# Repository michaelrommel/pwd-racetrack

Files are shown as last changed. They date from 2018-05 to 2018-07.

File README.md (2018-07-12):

# pwd-racetrack
A Pinewood Derby racetrack timer and start gate electronics circuits + firmware.

This software implements the firmware for a Pinewood Derby race track
electronics. The race track receives commands, like the setup or start commands
and sends back results, like the finishing times for each lane after a heat ends.

The racetrack electronics in the subdirectory circuits consists of three main parts:
- the main controller based on an Arduino Due with a protoype extension board.
  The extension board implements the connections to the finish line display
  modules and to the start gate.
- the display modules (one per lane) implement the main display of the achieved
  place in the heat and the display of the time in milliseconds. Also the LDR
  (Light Dependent Resistor) needed to detect the interruption of the laser
  beam is implemented on this module.
- the start gate electronics. This part is a separate Arduino Mega 2560
  controlling four RFID readers to detect the cars on each track, four OLED
  displays to shoe the car owner names and the solenoid for opening the start
  gate.

If you commit to this repo, please use descriptive commit messages. A good guide
can be found at: https://chris.beams.io/posts/git-commit/

In short, a properly formed Git commit subject line should always be able to 7
complete the following sentence:

- If applied, this commit will <_your subject line here_>

(c) 2018 by Michael Rommel

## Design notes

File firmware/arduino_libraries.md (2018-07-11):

## Libraries used for each firmware ##

### Finishline Controller ###

These Libraries are available from the library manager inside the Arduino IDE:

- FastLED 3.1.6
- ArduinoJSON 5.13.2

These libraries were copied from github repos and dropped into the firmware folder:

- https://github.com/RobTillaart/Arduino/raw/master/libraries/PCF8574/
- https://github.com/Seeed-Studio/Grove_4Digital_Display for TM1637 (Note: this library
has been modified by me)

### Startgate Controller ###

These Libraries are available from the library manager inside the Arduino IDE:

- U8g2 2.22.18
- MFRC522 1.3.6

The way to use the TCA9548A I2C multiplexer has been learned from this website:
https://learn.adafruit.com/adafruit-tca9548a-1-to-8-i2c-multiplexer-breakout/wiring-and-test

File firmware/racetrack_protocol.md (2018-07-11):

Pinewood Derby Racetrack Communication Protocol
===============================================

| Key | Value |
|---|---|
| Version | 0.7 |
| Date | 2018-07-11 |

## Overview ##

- strings may be at most 384 bytes long, that means, that JsonBuffer needs to
  be at least 601 bytes long, this is too large for the Pro mini, need to exchange
  only basic information between the controllers
- strings must be sent with a terminating linefeed \n, this is needed to ensure
  that only complete JSON messages are parsed.
- strings are sent repeatedly every 2 seconds until acknowledged without error
- strings are re-sent when acknowledged with error
- error messages are not acknowledged and not re-sent
- message ids are simple integer numbers and should be unique only from the
  perspective of the message creator
- Race track acknowledges commands as well
- RFIDs are normally between 4 bytes and 7 bytes long (Example UID: 04 57 57 A2 2D 4D 81 or UID: 7A 23 08 85)
- headlines indicate communication direction
  - C: Android / Raspberry / Operator PC as a Controller
  - R: Racetrack electronics
  - -> or <- denotes the direction of the communication

## JSON structure definition ##

### Global Message Structure ###

| Property | Shortname | Type | Required | Title |
|---|---|---|---|---|
| identifier | id | number | x | Message identifier, sequentially increasing |
| command | c | string | x | Command code, single character, unique across all defined message types |
| heat | h | number | x | Heat identifier, can be 0 if the message is not related to a running heat |
| status | s | number | | Status information, value depends on command |
| lanes | l | array  | | Array of objects related to information about all lanes |

### Table of Lane Object Properties ###

| Property | Shortname | Type | Required | Title |
|---|---|---|---|---|
| time | t | number | | Elapsed time of the car in this lane |
| rfid | rf | string | | RFID of the car in this lane |
| owner | ow | string | | Short name of the car owner (max. 14 characters) |
| model | mn | number | | Model identifier of the car (max. 8 digits, <100.000.000) |
| serial | sn | number | | Serial number of the car within the model line (max. 6 digits, <1.000.000) |
| laser | ll | number | | Laser light level as detected by the LDR sensor, helps setting up the track |

### Table of Status Codes ###

| Code | Description |
|---|---|
| 0 | Status OK |
| 1 | Heat setup completed |
| 2 | Heat in progress |
| 3 | Heat finished |
| 5 | Heat unknown |
| 6 | Correct lane |
| 7 | Wrong lane |
| 10 | Track Setup Start |
| 11 | Track Setup Report |
| 12 | Track Setup Stop |
| 1xx | Error Codes |
| 101 | Malformed JSON string |
| 102 | Invalid State transition |
| 103 | Invalid Command (for this partner or state) |

### Table of Command Codes ###

| Code | Direction | Description | Optional / Required Properties |
|---|---|---|---|
| a | both | Acknowledge a message | required: s |
| i | C -> R | Initialize a heat | required: l.rf, l.ow, l.mn, l.sn |
| g | C -> R | Go! Start a heat | - |
| p | R -> C | Progress report of a heat | required: s, l.t; optional: l.rf, l.mn, l.sn |
| d | R -> C | Detected the RFID of a new car in one of the lanes | required: s, l.rf; optional: l.mn, l.sn |
| c | R -> C | Completed the setup of a heat, all cars in place | required: s; optional: l.id, l.mn, l.sn |
| s | C -> R | Set up the racetrack to adjust the lasers | required: s |
| l | R -> C | Laser measurement report for setup | required: s, l.ll |

### Table of Program States ###

| State | Description | Possible Next States | Accepts Messages | Emits Messages |
|---|---|---|---|---|
| Idle | Track is waiting to receive next heat configuration | Heat Setup, Track Setup | INIT, SETUP (start) | DETECT |
| Heat Setup  | Track is waiting for lanes to be populated | Heat Setup, Track Setup, Racing | INIT, SETUP (start), GO  | DETECT, COMPLETE | 
| Track Setup | Track is calibrating the lasers | Idle, Heat Setup | SETUP (stop) | LASER |
| Racing | Heat is in progress | Idle | - | PROGRESS |

## Examples of messages ##

### Normal JSON message acknowledgments ###

A correctly received message shall be indicated to the other end.
The limited amount of Arduino memory can only store 2-3 unacknowledged
messages. A message that has not been acknowledged within 2 seconds shall
be retransmitted.

```
{
  "id" : 11,      // This is the id of the received message
  "c" : "a",
  "s" : 0         // OK
}
```

### Error JSON Malformed acknowledgments ###

Retransmission of the message with the mentioned `id` should be initiated immediately,
the sending side shall not wait for a timeout.

```
{
  "id" : 0,       // Use 0 because of corrupted message
  "c" : "a",
  "s" : 101       // Maybe a character was dropped during transmission
}
```

### Error Invalid State Transition acknowledgments ###

No retransmission of the message with the mentioned `id` is needed, because the requested
state transition is invalid. 

```
{
  "id" : 11,      // This is the id of the received message
  "c" : "a",
  "s" : 102       // e.g. requesting a heat start, when there is still one running
}
```

### Error Invalid Command ###

No retransmission of the message with the mentioned `id` is needed, because the sent
command is invalid for this state or not allowed from this communication partner

```
{
  "id" : 11,      // This is the id of the received message
  "c" : "a",
  "s" : 103       // e.g. requesting a heat start, when there is still one running
}
```

### Start the setup the racetrack ###

```
{
  "id" : 11,
  "c" : "s",
  "h" : 0,
  "s" : 10
}
```

### Stop the setup the racetrack ###

```
{
  "id" : 12,
  "c" : "s",
  "h" : 0,
  "s" : 12
}
```

### Initialize a heat ###

```
{
  "id" : 13,
  "c" : "i",
  "h" : 7,
  "l" : [
    { "rf" : "045F57A22D4D81",
      "ow" : "Kara Thrace",
      "mn" : 1234567,
      "sn" : 42 },
    { "rf" : "03857FAD2D4D74",
      "ow" : "Lee Adama",
      "mn" : 1234567,
      "sn" : 35 },
    { "rf" : "156F78DA2D6582",
      "ow" : "Sharon Valerii",
      "mn" : 1234567,
      "sn" : 24 },
    { "rf" : "669EBCC390DA03",
      "ow" : "Karl Agathon",
      "mn" : 1234567,
      "sn" : 45 }
  ]
}
```

### Start a Heat ###

```
{
  "id" : 14,
  "c" : "g",
  "h" : 7
}
```

### Detection of a car (no heat was set up) ###

The startgate can sense an RFID and report it at any time. This is then sent
with the status code for `Heat unknown` and a heat number of `0`. The lanes
array contains emtpy objects for lanes where there was no car detected. 
Naturally, no name or other car information can be determined.

```
{
  "id" : 20,
  "c" : "d",
  "h" : 0,
  "s" : 5,
  "l" : [
    {}, 
    { "rf" : "156F78DA2D6582" },
    {},
    {}
  ]
}
```

### Detection of a car (heat was initialized, correct lane) ###

The startgate sensed a car in the correct lane.

```
{
  "id" : 21,
  "c" : "d",
  "h" : 21,
  "s" : 6,
  "l" : [
    {}, 
    {},
    { "rf" : "156F78DA2D6582",
      "ow" : "Sharon Valerii",
      "mn" : 1234567,
      "sn" : 24 },
    {}
  ]
}
```

### Detection of a car (heat was initialized, wrong lane) ###

The startgate sensed a car in the wrong lane.

```
{
  "id" : 22,
  "c" : "d",
  "h" : 21,
  "s" : 7,
  "l" : [
    {}, 
    {},
    {},
    { "rf" : "156F78DA2D6582",
      "ow" : "Sharon Valerii",
      "mn" : 1234567,
      "sn" : 24 }
  ]
}
```

### Detection of all cars of a heat in the correct lanes ###

The startgate marks this heat as correctly set up. An empty object in a lane
is not necessarily an error, this lane may be left empty for this heat.

```
{
  "id" : 23,
  "c" : "c",
  "h" : 24,
  "s" : 1,
  "l" : [
    { "rf" : "045F57A22D4D81",
      "ow" : "Kara Thrace",
      "mn" : 1234567,
      "sn" : 42 },
    { "rf" : "03857FAD2D4D74",
      "ow" : "Lee Adama",
      "mn" : 1234567,
      "sn" : 35 },
    {},
    { "rf" : "669EBCC390DA03",
      "ow" : "Karl Agathon",
      "mn" : 1234567,
      "sn" : 45 }
  ]
}
```

### Progress report of a heat (still running) ###

One or more cars have finished the heat, but not all. The heat is still
in progress.

```
{
  "id" : 30,
  "c"  : "p",
  "h"  : 24,
  "s"  : 2,
  "l"  : [
    { "t"  : 2345,
      "rf" : "045F57A22D4D81",
      "ow" : "Kara Thrace",
      "mn" : 1234567,
      "sn" : 42 },
    {},
    {},
    { "t"  : 3456,
      "rf" : "669EBCC390DA03",
      "ow" : "Karl Agathon",
      "mn" : 1234567,
      "sn" : 45 }
  ]
}
```

### Progress report of a finished heat ###

All cars have finished or the maximum time has been reached.
For all initialized cars, at least the `time` field has to be reported.
For cars that fail to reach the finish line, the timeout time is 
reported. 

```
{
  "id" : 32,
  "c" : "p",
  "h" : 24,
  "s" : 3,
  "l" : [
    { "t"  : 1234,
      "rf" : "045F57A22D4D81",
      "ow" : "Kara Thrace",
      "mn" : 1234567,
      "sn" : 42 },
    { "t"  : 7777,
      "rf" : "03857FAD2D4D74",
      "ow" : "Lee Adama",
      "mn" : 1234567,
      "sn" : 35 },
    {},
    { "t"  : 3456,
      "rf" : "669EBCC390DA03",
      "ow" : "Karl Agathon",
      "mn" : 1234567,
      "sn" : 45 }
  ]
}
```

### Laser setup measurements ###

During construction of the racetrack on race day, the lasers of the 
finishing line might need adjustment. So once the `setup` mode is
initialized, the track reports the analogRead value of the LDR pin
for each lane. This helps adjusting the optimal beam of light.

```
{
  "id" : 40,
  "c" : "l",
  "h" : 0,
  "s" : 11,
  "l" : [
    { "ll"  : 852 },
    { "ll"  : 749 },
    { "ll"  : 822 },
    { "ll"  : 878 }
  ]
}
```

## Changelog ##

0.7
- changed full name to short name, because we can at max. display 14 characters
- changed max length of short name to 14

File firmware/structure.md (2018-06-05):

Class for a lane
==================

- initialize with address of PCA9501D
- method to set the 4 digits of the TM1637
- method to set the large digit
- method to query the value of the LDR
- method to query the triggering of a stop
- method to reset the trigger

Class for Message ???
=================

Class for a Heat
================

- method to initialize the heat with a number of lanes
- method to start the heat, block incoming serials
- method to query the progress / status
- method to end the heat, release the incoming serial block

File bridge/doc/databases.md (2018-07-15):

Pinewood Derby Bridge Database Structures
=========================================

| Key | Value |
|---|---|
| Version | 0.3 |
| Date | 2018-07-11 |

## Overview ##

## DB structure definition ##

### Race Database ###

The database shall hold the basic information about a race. The whole race is
contained in one key, which is typically the year, followed by a string identifying
the race or demonstration etc. 

Properties of the race are:

| Property | Type | Description |
|---|---|---|
| description | string | description of this race setup |
| lanes | number | number of lanes of the race track |
| heatsQuali | number | number of heats in the qualification round |
| heatsFinals | number | number of heats in the final round |
| finalCarCount  | number | how many cars are in the final round |
| cars | object | car object with all cars in this race |

Properties of the car object are:

| Property | Type | Description |
|---|---|---|
| \<startnumber\> | string | uuid or other key from the Car Database |

#### Example ####

```
Key:
  "2018-Race"
Value:
  {
    "description": "Demo race at the event xxx",
    "lanes": 4,
    "heatsQuali": 33,
    "heatsFinals": 14,
    "finalCarCount": 7,
    "cars" : {
      "1": "043E57A22D4D80",
      "2": "048756A22D4D80",
      "3": "048F56A22D4D80"
      ...
    }
  }
```

### Car Database ###

The database shall hold the basic information about each car. The key should be 
a UUID identifier or a RFID, whichever is more suitable.

Properties of the car are:

| Property | Type | Description |
|---|---|---|
| rf | string | RFID of the car |
| ow | string | Short name of the car owner (max. 14 characters) |
| name | string | Full name of the car owner |
| country | string | Country name of the car owner |
| mn | number | Model identifier of the car (max. 8 digits, <100.000.000) |
| sn | number | Serial number of the car within the model line (max. 6 digits, <1.000.000) |

#### Example ####

```
Key:
  "048756A22D4D80"
Value:
  {
    "rf": "048756A22D4D80",
    "ow": "Kara",
    "name": "Kara Thrace",
    "country": "Caprica",
    "mn": 201807181,
    "sn": 113
  }
```

### Race Config Database ###

The database shall hold the lane assignments for races with a predfined number of participants.
The number of cars equals the number of heats. Currently we store only configs for 4 lanes.
The key is the number of lanes followed by a minus sign and the number of cars/heats.

The value of a raceconfig is an object with an heats object describing for each heat
which cars are on each lane.

Properties of a race configuration

| Property | Type | Description |
|---|---|---|
| description | String | description of this configuration |
| heats | Object | contains a heat configuration object |

Properties of each heat config object are:

| Property | Type | Description |
|---|---|---|
| \<heatnumber\> | Array  | contains a lane array |

Lane array members:

| Property | Type | Description |
|---|---|---|
| \<carnumber\>  | Number | startnumber of a car that starts in the lane |

#### Example ####

```
Key:
  "4-36"
Value:
  { "description": "Partial Perfect 4 Lanes, 36 cars config",
    "heats" : {
      "1":  [  1,  3,  6, 10],
      "2":  [  2,  4,  7, 11],
      "3":  [ 12, 14, 17, 21], 
      "4":  [ 13, 15, 18, 22],
      "5":  [ 23, 25, 28, 32],
      "6":  [ 24, 26, 29, 33],
      "7":  [ 25, 27, 30, 34],
      "8":  [ 36,  2,  5,  9],
      "9":  [ 11, 13, 16, 20],
      "10": [ 26, 28, 31, 35],
      "11": [  3,  5,  8, 12],
      "12": [ 14, 16, 19, 23],
      "13": [ 15, 17, 20, 24],
      "14": [ 27, 29, 32, 36],
      "15": [ 35,  1,  4,  8],
      "16": [  5,  7, 10, 14],
      "17": [  4,  6,  9, 13],
      "18": [ 16, 18, 21, 25],
      "19": [ 17, 19, 22, 26],
      "20": [ 28, 30, 33,  1],
      "21": [ 29, 31, 34,  2],
      "22": [  6,  8, 11, 15],
      "23": [ 18, 20, 23, 27],
      "24": [ 30, 32, 35,  3],
      "25": [  7,  9, 12, 16],
      "26": [ 19, 21, 24, 28],
      "27": [ 31, 33, 36,  4],
      "28": [  8, 10, 13, 17],
      "29": [ 20, 22, 25, 29],
      "30": [ 32, 34,  1,  5],
      "31": [  9, 11, 14, 18],
      "32": [ 10, 12, 15, 19],
      "33": [ 21, 23, 26, 30],
      "34": [ 22, 24, 27, 31],
      "35": [ 33, 35,  2,  6],
      "36": [ 34, 36,  3,  7]
    }
  }

```

### Heat Database ###

The database shall hold information about each heat. It gets preconfigured when a race
is set up with the cars. The key is the ID from the race combined with a minus
sign, followed by the heatnumber in this race. The heatnumbers in a race start
with 1 (not zero).
 
Properties of each heat are:

| Property | Type | Description |
|---|---|---|
| heat | number | number of the heat in the race |
| status | string | status field indicating the state of this heat |
| results | array  | an array of 4 lane results |

Possible values for the status field are:

| Value | Description |
|---|---|
| finished | this heat has completed, results are in |
| running | the cars in this heat are currently racing |
| current | this is the current heat, but race has not started  |
| next | this is the next heat that has been prepared |

Properties of a lane result object:

| Property | Type | Description |
|---|---|---|
| rf | string | RFID of the car in this lane |
| ow | string | short name of the car owner (max. 14 characters) |
| mn | number | model identifier of the car (max. 8 digits, <100.000.000) |
| sn | number | serial number of the car within the model line (max. 6 digits, <1.000.000) |
| t | number | time in milliseconds the car needed for this run |
| score | number | the score, that this car got for the place in this run |

#### Example ####

```
Key:
  "2018-Race-07"
Value:
  {
    "heat": 7,
    "status": "finished",
    "results" : [
      {"rf":"044E57A22D4D","ow":"Kara Thrace","mn":201807181,"sn":14,"t":5455,"score":1},
      {"rf":"045657A22D4D","ow":"Lee Adama","mn":201807181,"sn":28,"t":3440,"score":8},
      {"rf":"04E556A22D4D","ow":"Sharon Valerii","mn":201807181,"sn":9,"t":3729,"score":2},
      {"rf":"047756A22D4D","ow":"Karl Agathon","mn":201807181,"sn":22,"t":3671,"score":4}
    ]
  }
```

### Leaderboard Database ###

The database shall hold information about all the participants in the race.
The value is an dictionary of all participants as Objects with the car ID
as key. Each participant has fields for the score and cumulated time during
the qualification round and the finals. The key is the ID from the race.
 
Properties of each race entry are car objects:

| Property | Type | Description |
|---|---|---|
| \<car rfid\> | Object | contains a car object |

Properties of a car object:

| Property | Type | Description |
|---|---|---|
| rf | string | RFID of the car in this lane |
| ow | string | short name of the car owner (max. 14 characters) |
| mn | number | model identifier of the car (max. 8 digits, <100.000.000) |
| sn | number | serial number of the car within the model line (max. 6 digits, <1.000.000) |
| cumTmeQuali | number | cumulated time in milliseconds of all heats this car has completed up to now during qualification |
| cumScoreQuali  | number | cumulated score of this car in the qualification |
| cumTimeFinals  | number | cumulated time in milliseconds of all heats this car has completed up to now during finals |
| cumScoreFinals | number | cumulated score of this car in the finals |

#### Example ####

```
Key:
  "2018-Race"
Value:
  {
    { "04A256A22D4D": {
        "rf":"04A256A22D4D",
        "ow":"Louanne Katraine",
        "mn":"201807181",
        "sn":"1200",
        "cumTimeQuali":0,
        "cumScoreQuali":0,
        "cumTimeFinals":0,
        "cumScoreFinals":0 } 
    },
    { "047756A22D4D": {
        "rf":"047756A22D4D",
        "ow":"Margaret Edmondson",
        "mn":"201807181",
        "sn":"1209",
        "cumTimeQuali":3671,
        "cumScoreQuali":8,
        "cumTimeFinals":0,
        "cumScoreFinals":0 }
    },
    { "045B56A22D4D": {
        "rf":"045B56A22D4D",
      ... }
  }      
  
```

### Highscore Database ###

The database shall hold information about the 20 track records, the fastest
times that these cars have achieved. A car can be in the higscore table multiple
times. The value is an array of rank objects. The key is the ID from the race.
 
Properties of a rank object:

| Property | Type | Description |
|---|---|---|
| rf | string | RFID of the car in this lane |
| ow | string | short name of the car owner (max. 14 characters) |
| mn | number | model identifier of the car (max. 8 digits, <100.000.000) |
| sn | number | serial number of the car within the model line (max. 6 digits, <1.000.000) |
| t | number | time in milliseconds this car has had in the heat, that made it into the highscore |
| score | number | the score that the car got in this heat |
| heat | string | the identifier of the heat, where the car achieved the highscore |
| rank | number | the rank of this entry (not needed, if this is already the property of this entry) |

#### Example ####

```
Key:
  "2018-Race"
Value:
  [
    {
      "rf":"04A256A22D4D",
      "ow":"Louanne Katraine",
      "mn":"201807181",
      "sn":"1200",
      "t": 3671,
      "score":8,
      "heat":"2018-Race-00",
      "rank":1 },
    {
      "rf":"047756A22D4D",
      "ow":"Margaret Edmondson",
      "mn":"201807181",
      "sn":"1209",
      "t":3690,
      "score":8,
      "heat":"2018-Race-05",
      "rank":2 },
    {
      "rf":"045B56A22D4D",
      ... }
  ]      

```

## Changelog ##

0.3
- added race description
- added heat configuration description

0.2
- fixed typos
- changed highscore to revert back to flat array of objects

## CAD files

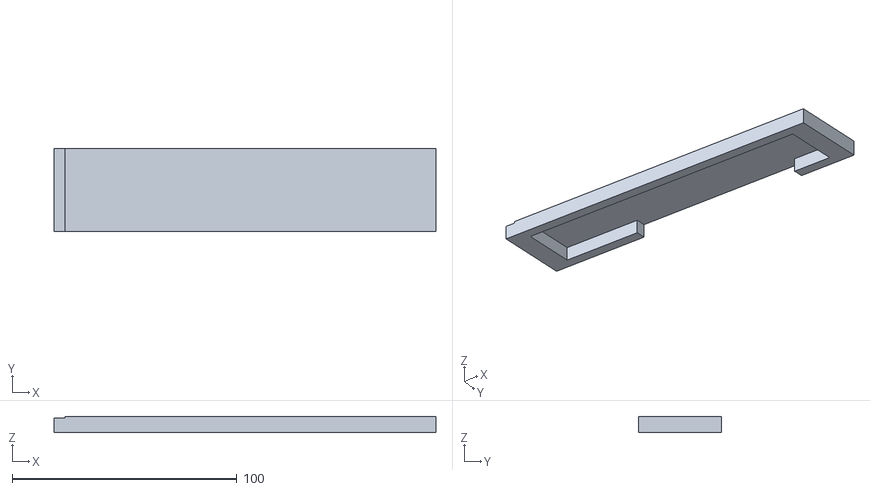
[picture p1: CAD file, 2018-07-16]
hardware/Made-Cover-right.stl
170.0 x 37.0 x 7.30

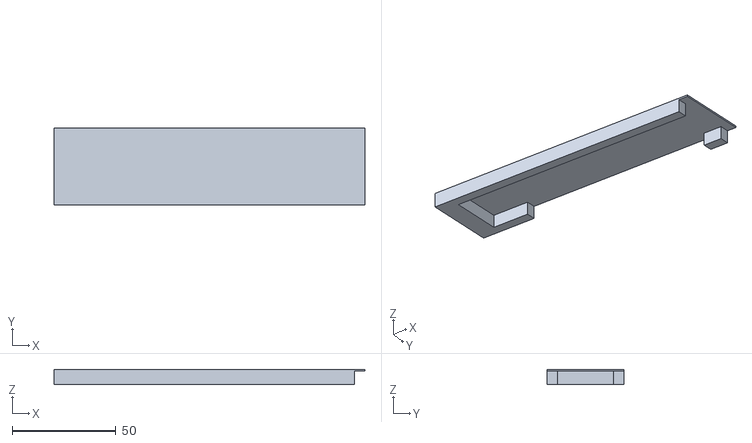
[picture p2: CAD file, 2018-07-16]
hardware/Made-Cover-left.stl
150.0 x 37.0 x 7.30

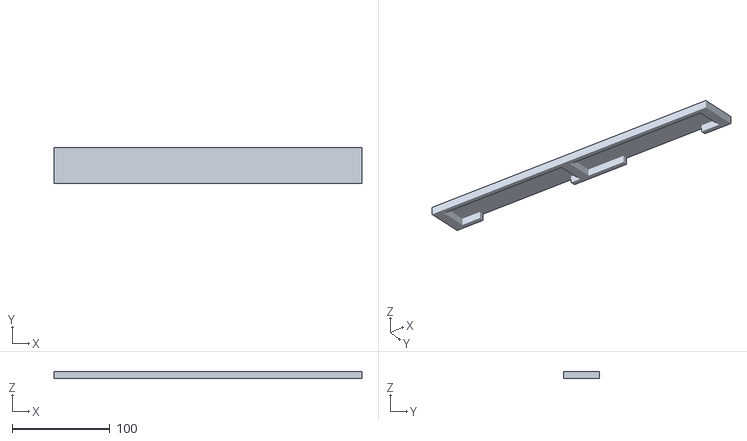
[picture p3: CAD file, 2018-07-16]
hardware/Made With - Cover.stl
315.0 x 37.0 x 7.30

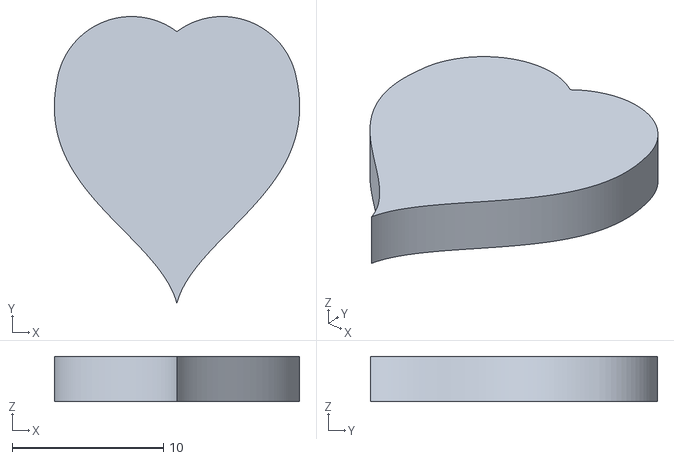
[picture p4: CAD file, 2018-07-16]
hardware/Herzchen.stl
16.2 x 19.0 x 3.00

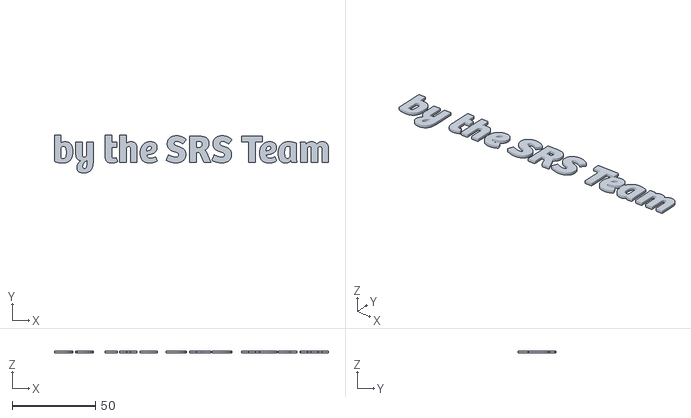
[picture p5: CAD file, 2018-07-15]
hardware/by the SRS Team.stl
164.6 x 22.9 x 1.50

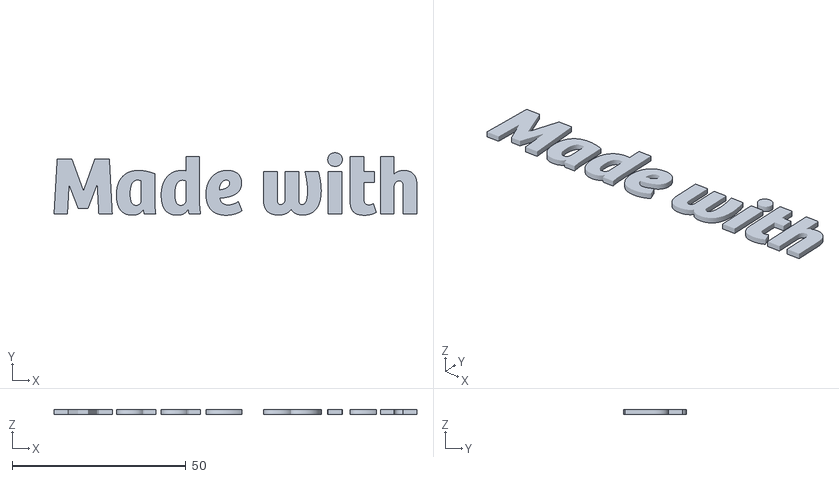
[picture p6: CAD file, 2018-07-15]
hardware/Made With.stl
104.6 x 18.0 x 1.50

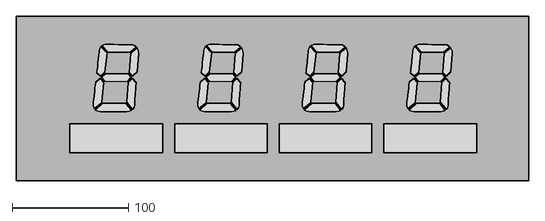
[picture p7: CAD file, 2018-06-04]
hardware/Finishline-Display-Transluzent.dxf
441.3 x 141.3

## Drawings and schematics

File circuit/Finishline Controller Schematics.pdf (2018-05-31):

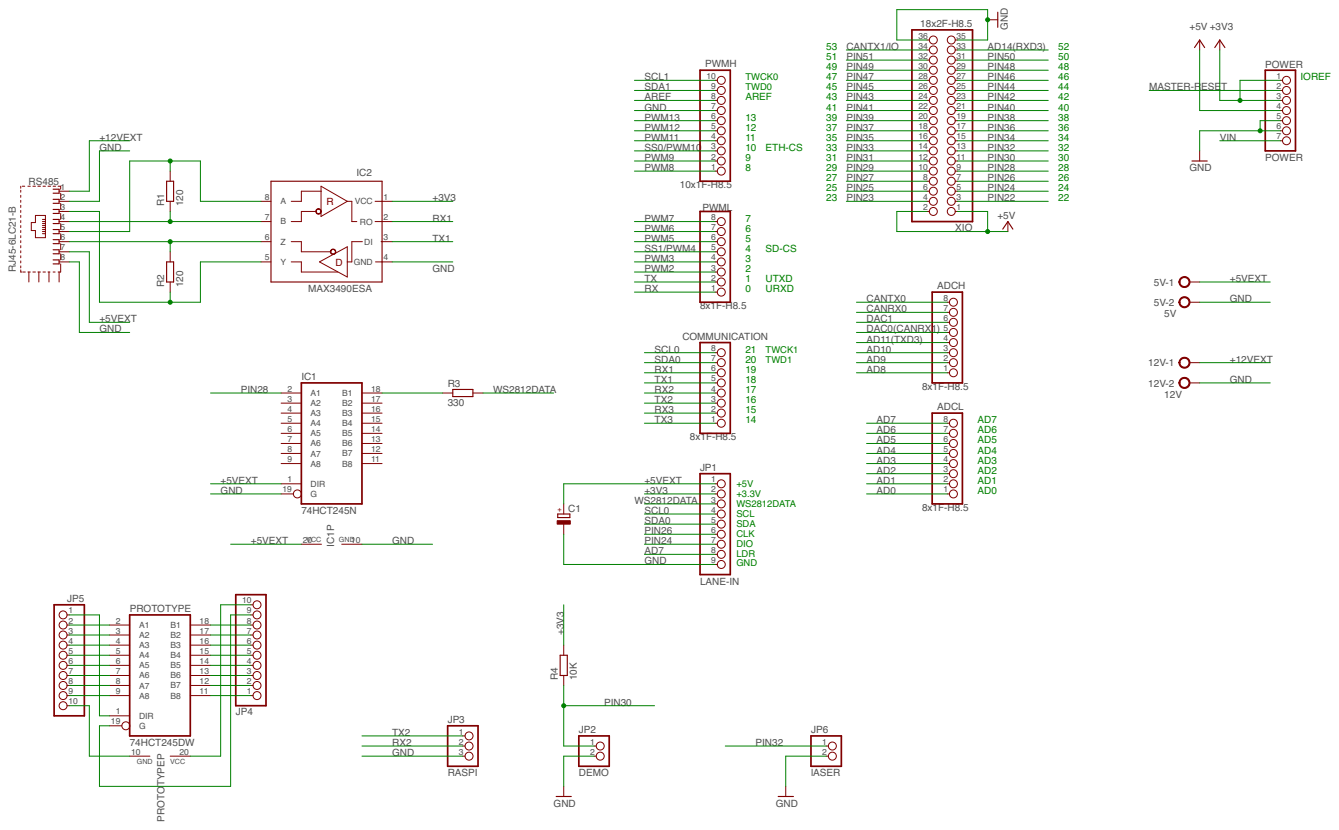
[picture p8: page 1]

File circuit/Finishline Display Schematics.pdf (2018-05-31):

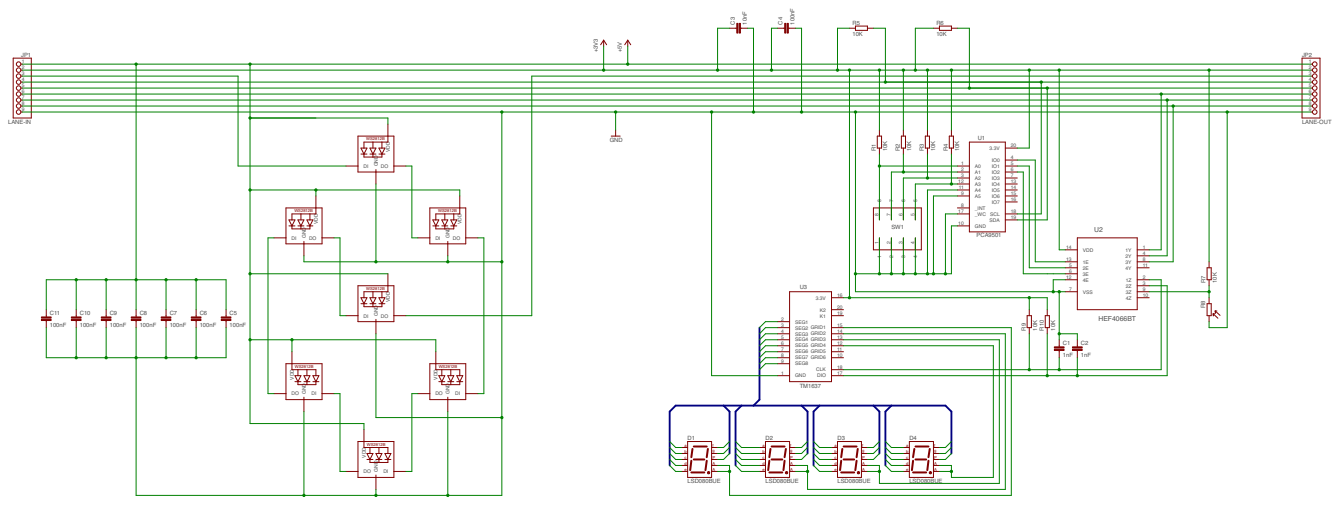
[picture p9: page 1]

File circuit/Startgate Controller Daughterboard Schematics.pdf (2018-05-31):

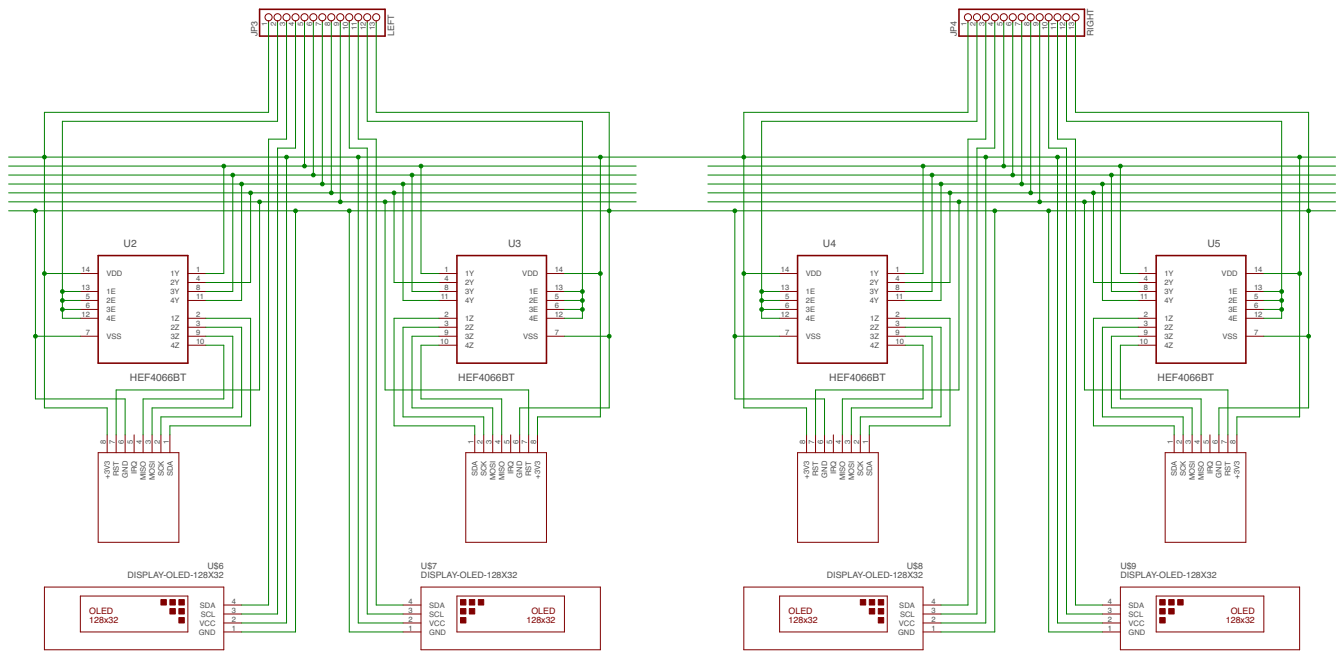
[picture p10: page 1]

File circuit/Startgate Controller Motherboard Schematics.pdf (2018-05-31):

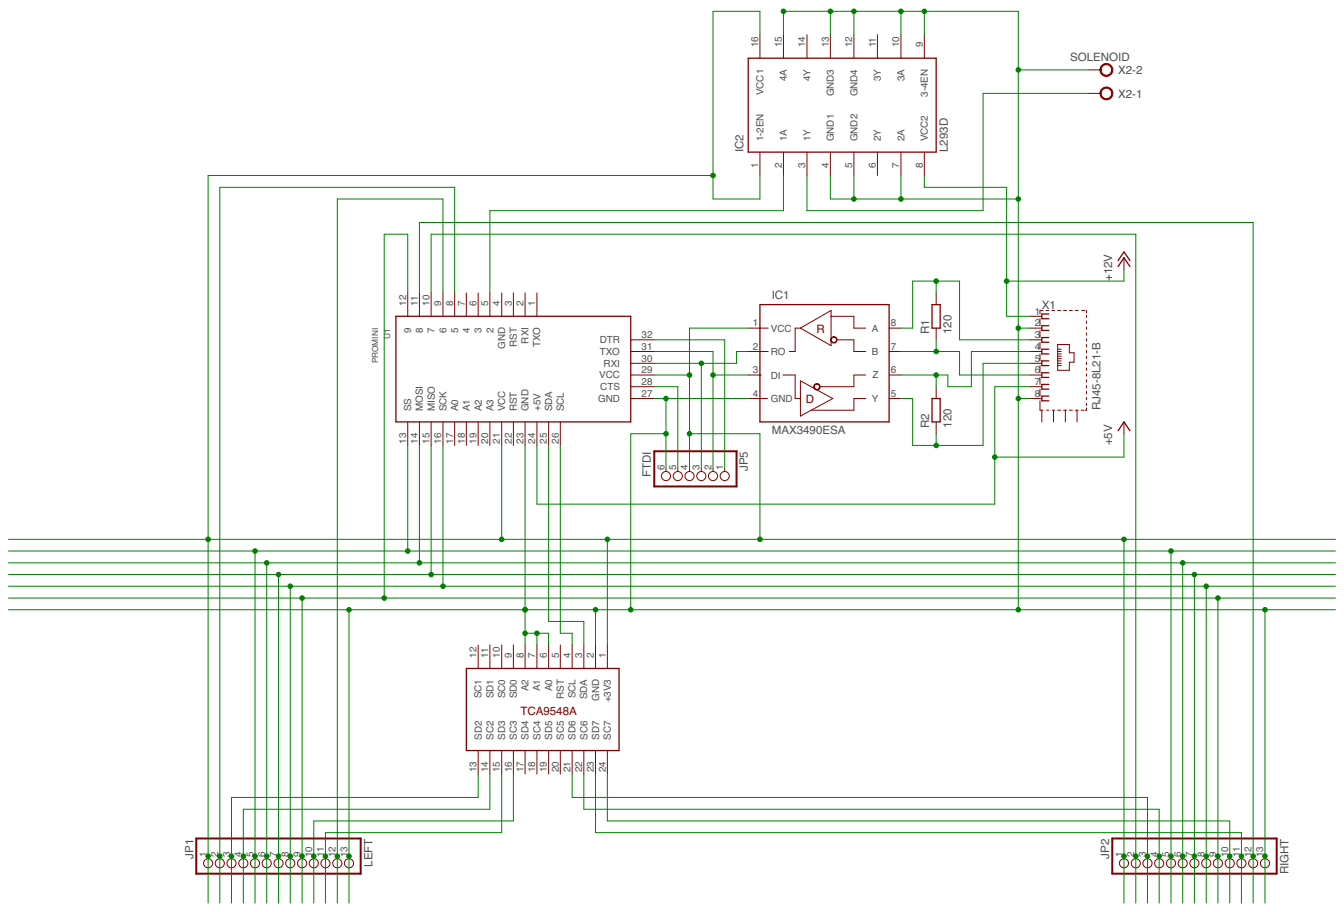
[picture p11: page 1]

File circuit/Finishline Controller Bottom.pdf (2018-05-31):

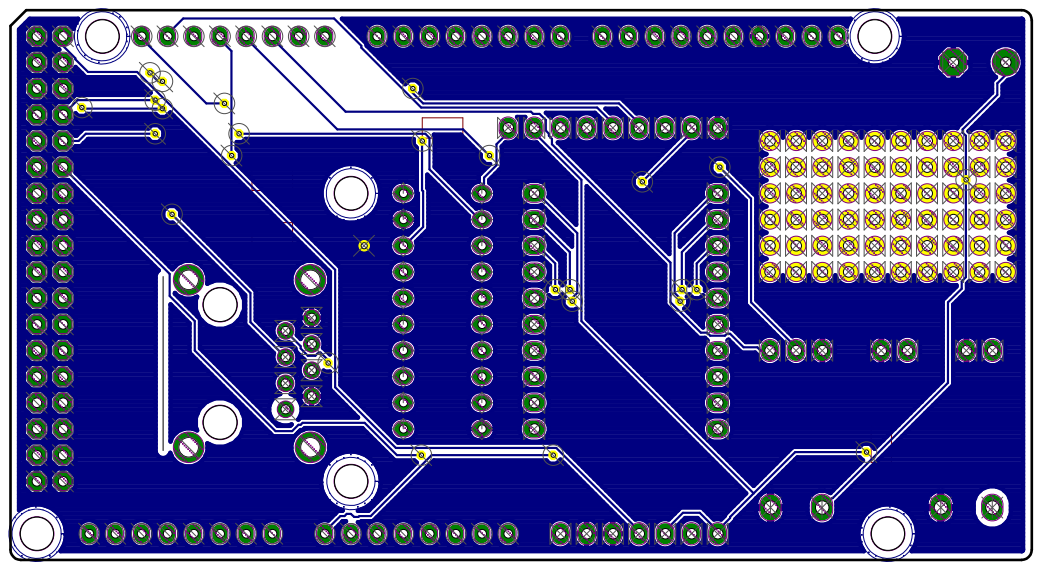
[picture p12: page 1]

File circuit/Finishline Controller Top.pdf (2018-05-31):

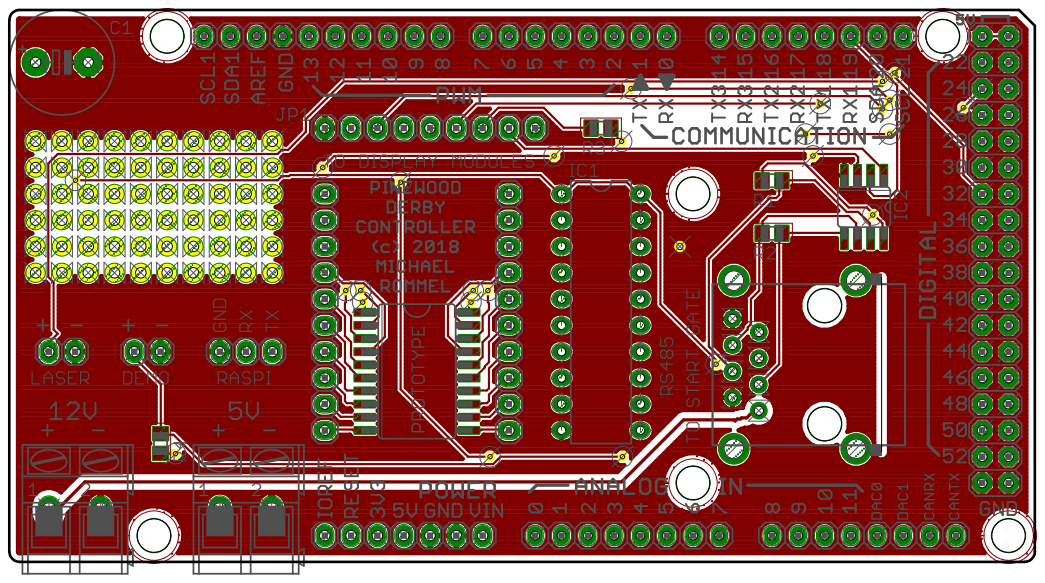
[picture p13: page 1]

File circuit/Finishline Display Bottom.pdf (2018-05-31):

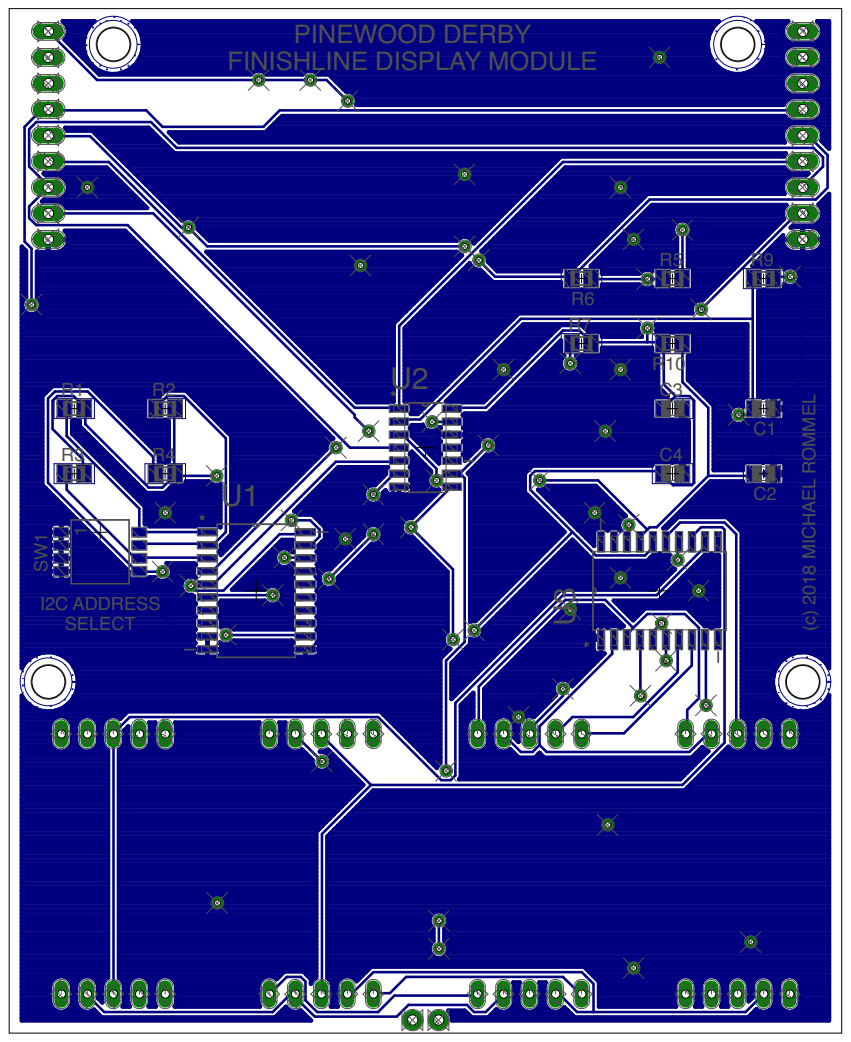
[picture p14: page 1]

SELECT | * | U1

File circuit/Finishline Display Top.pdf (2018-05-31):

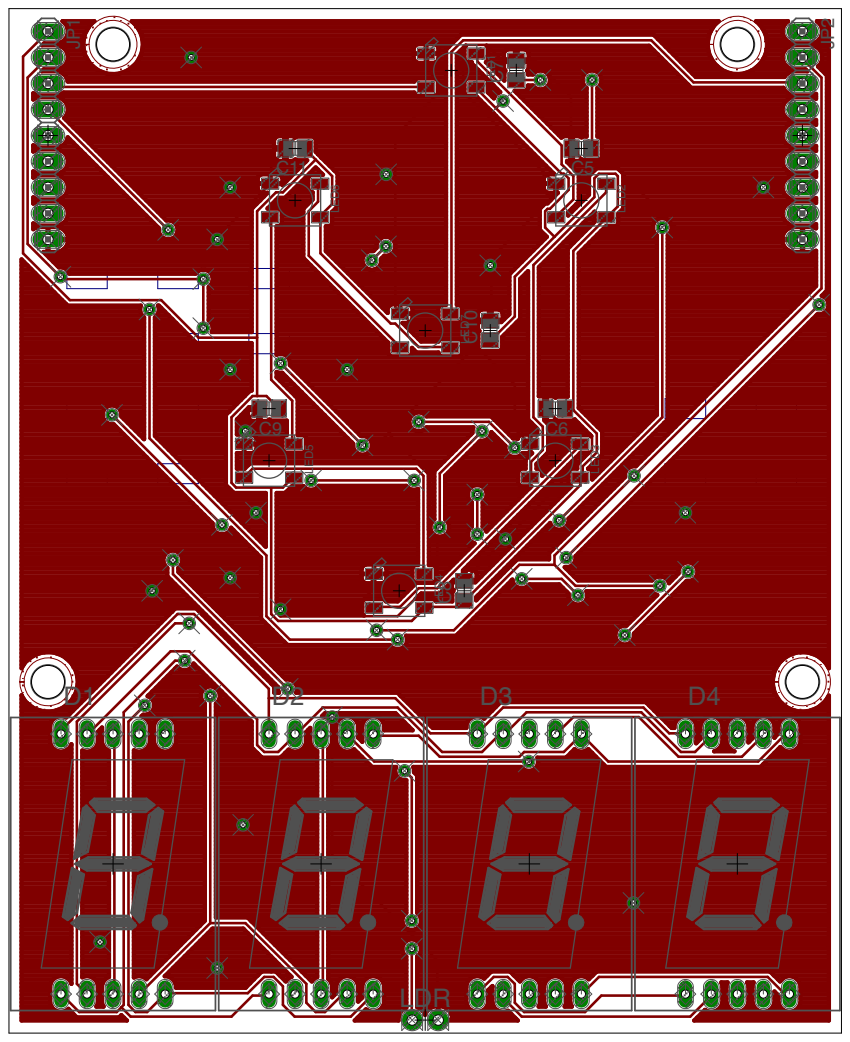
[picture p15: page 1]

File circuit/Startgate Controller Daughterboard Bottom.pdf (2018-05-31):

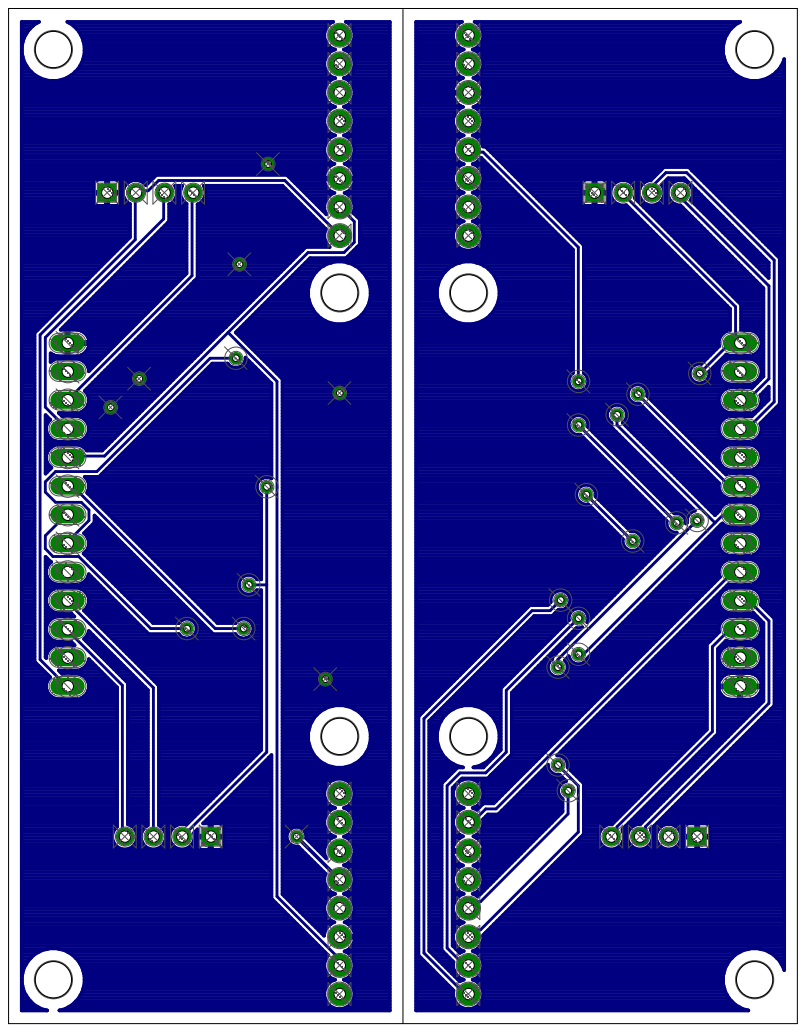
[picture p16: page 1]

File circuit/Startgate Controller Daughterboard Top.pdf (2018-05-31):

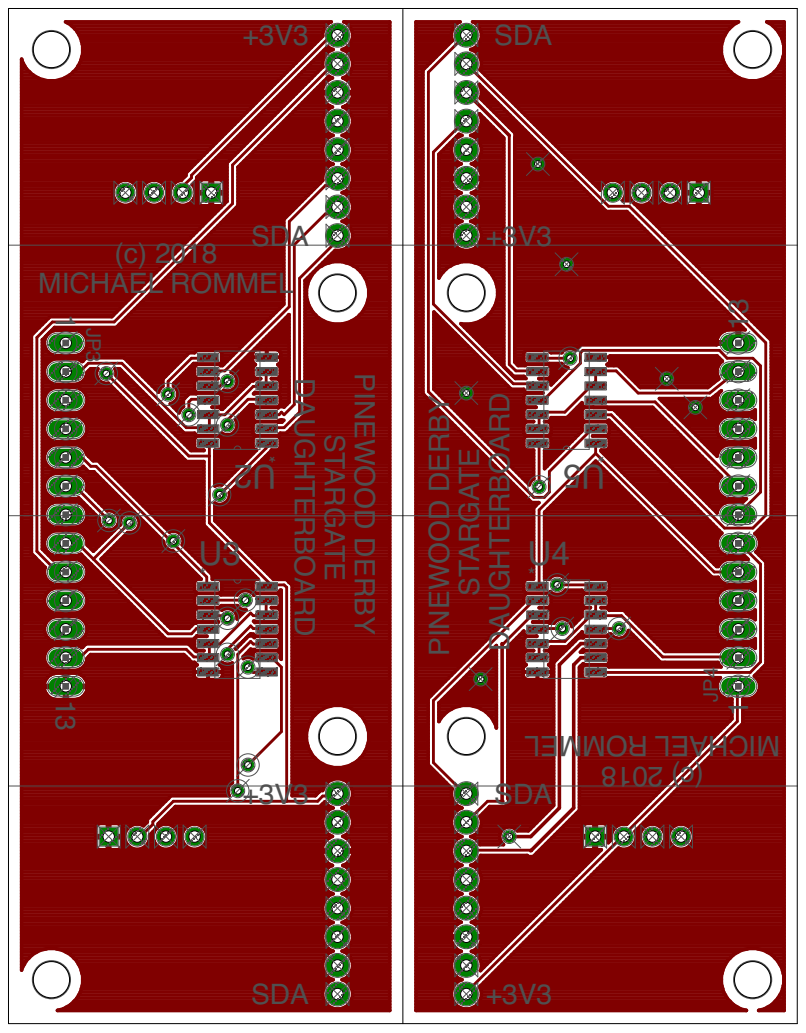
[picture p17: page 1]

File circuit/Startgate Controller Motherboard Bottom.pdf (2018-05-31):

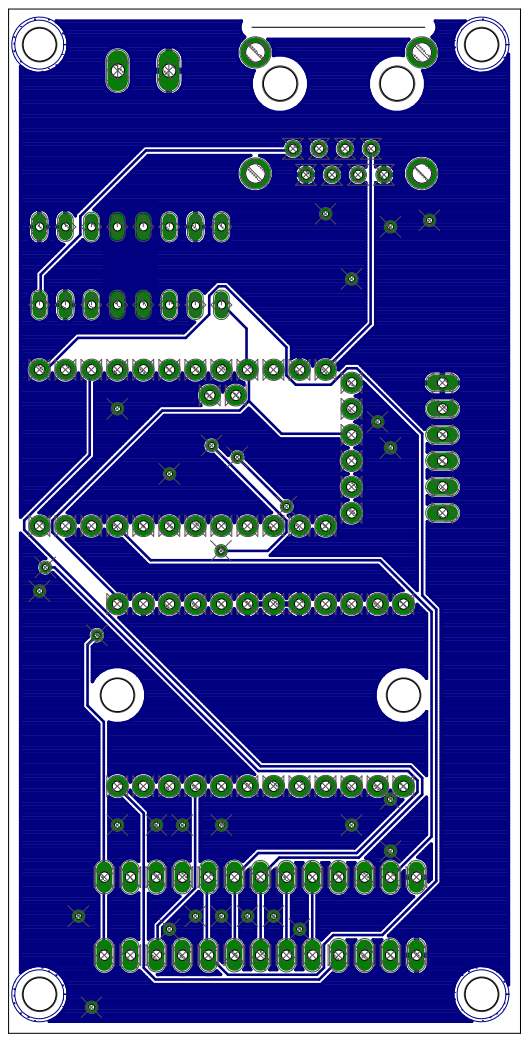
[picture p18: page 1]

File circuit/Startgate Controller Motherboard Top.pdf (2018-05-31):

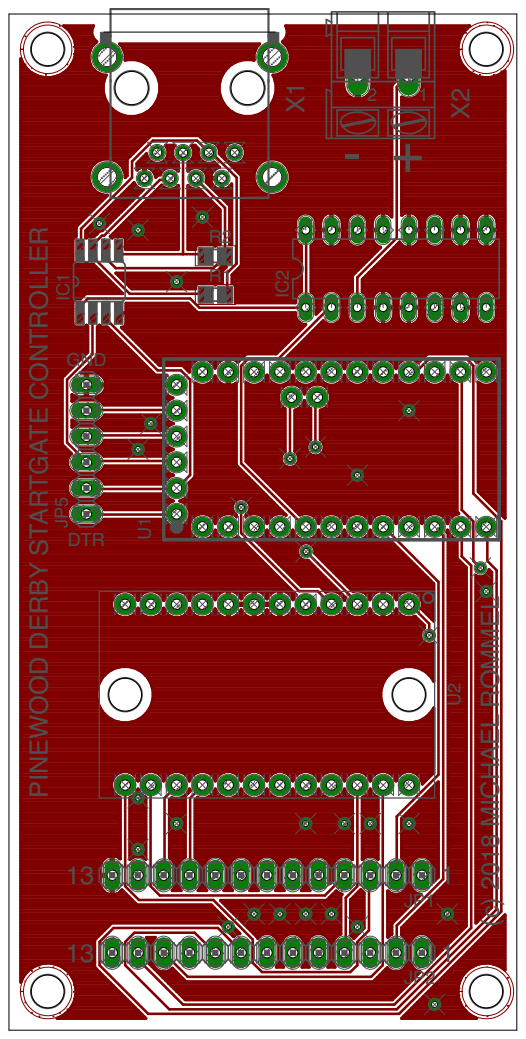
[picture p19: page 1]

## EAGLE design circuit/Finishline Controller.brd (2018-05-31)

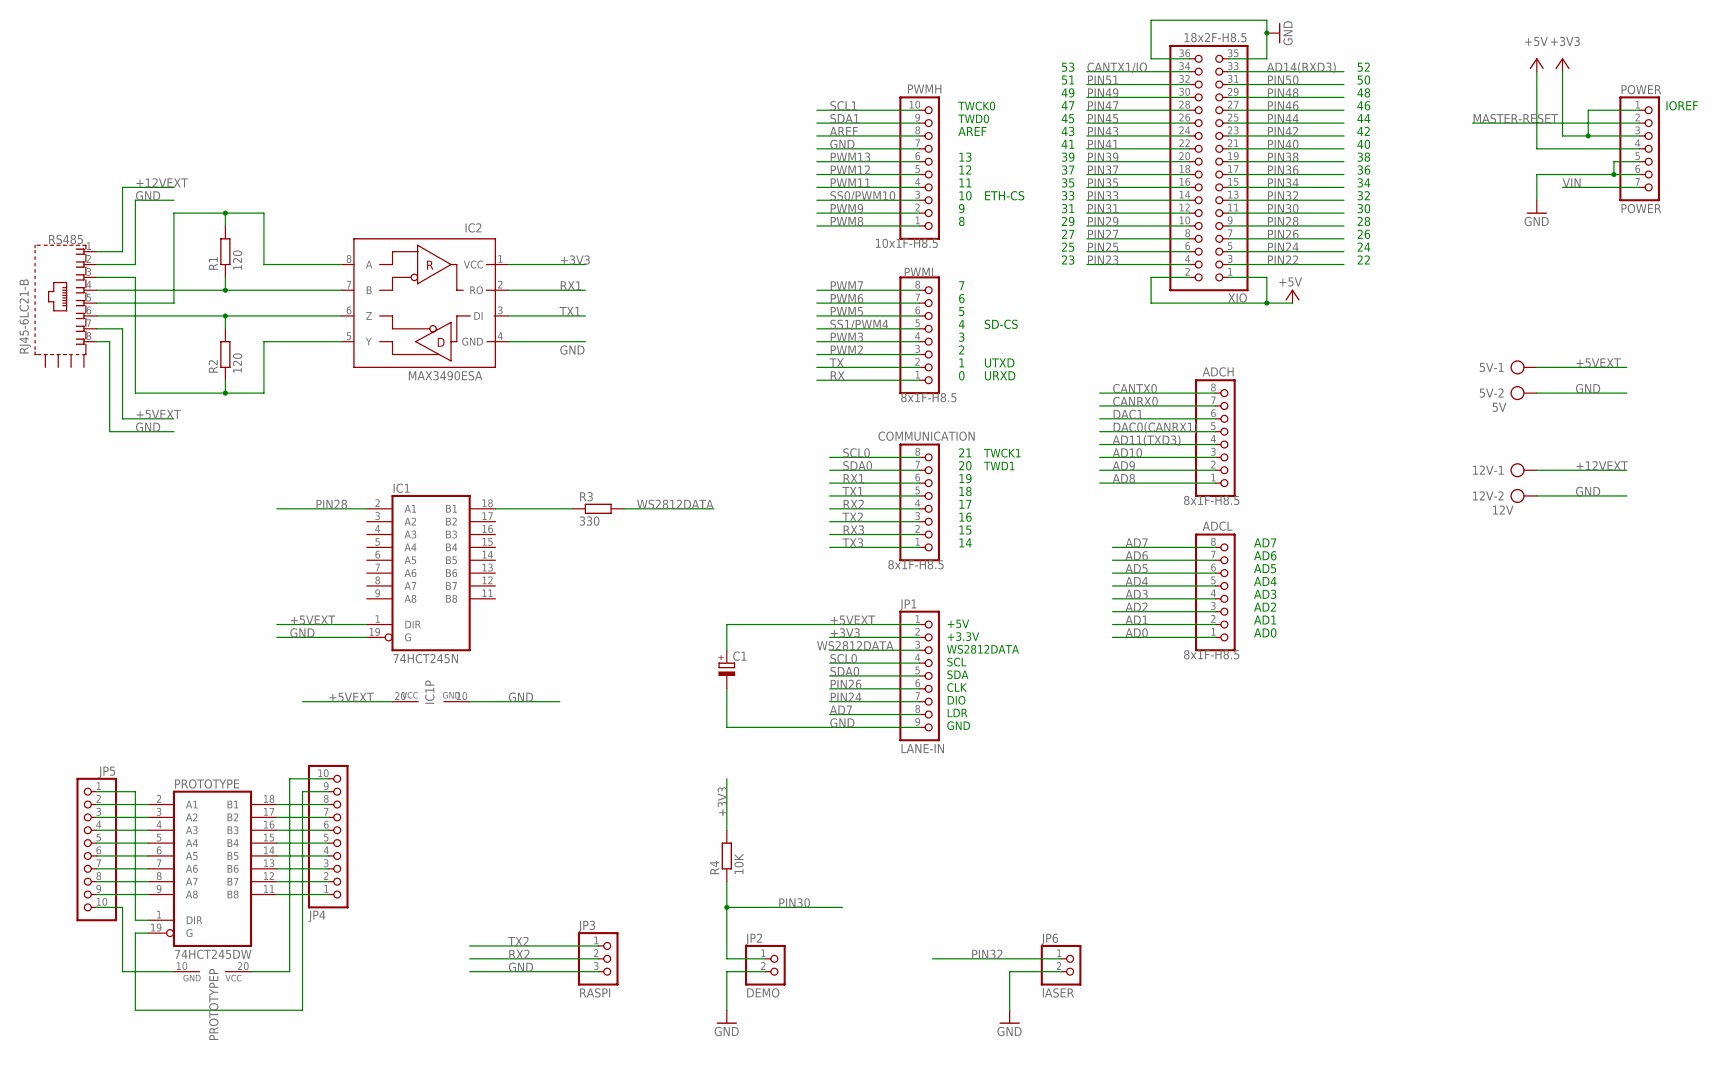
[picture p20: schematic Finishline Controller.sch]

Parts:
5V: 5V; AK300/2
12V: 12V; AK300/2
ADCH: 8x1F-H8.5; 1X08
ADCL: 8x1F-H8.5; 1X08
C1: CPOL-EUE5-10.5; E5-10,5
COMMUNICATION: 8x1F-H8.5; 1X08
IC1: 74HCT245N; DIL20
IC2: MAX3490ESA; SO08
JP1: LANE-IN; 1X09
JP2: DEMO; 1X02
JP3: RASPI; 1X03
JP4, JP5: PINHD-1X10; 1X10
JP6: lASER; 1X02
POWER: POWER; 1X07
PROTOTYPE: 74HCT245DW; SO20W
PWMH: 10x1F-H8.5; 1X10
PWML: 8x1F-H8.5; 1X08
R1, R2: 120; R0805
R3: 330; R0805
R4: 10K; R0805
RS485: RJ45-6LC21-B; RJ45-SHIELD1
XIO: 18x2F-H8.5; 2X18

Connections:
+3V3: IC2.1 (VCC), JP1.2, POWER.1, POWER.3, R4.2
+5V: POWER.4, XIO.1, XIO.2
+5VEXT: 5V.1, C1.+, IC1.1 (DIR), IC1.20 (VCC), JP1.1, RS485.7
+12VEXT: 12V.1, RS485.1
AD0: ADCL.1
AD1: ADCL.2
AD2: ADCL.3
AD3: ADCL.4
AD4: ADCL.5
AD5: ADCL.6
AD6: ADCL.7
AD7: ADCL.8, JP1.8
AD8: ADCH.1
AD9: ADCH.2
AD10: ADCH.3
AD11(TXD3): ADCH.4
AD14(RXD3): XIO.33
AREF: PWMH.8
CANRX0: ADCH.7
CANTX0: ADCH.8
CANTX1/IO: XIO.34
DAC0(CANRX1): ADCH.5
DAC1: ADCH.6
GND: 5V.2, 12V.2, C1.-, IC1.10 (GND), IC1.19 (G), IC2.4 (GND), JP1.9, JP2.2, JP3.3, JP6.2, POWER.5, POWER.6, PWMH.7, RS485.2, RS485.8, XIO.35, XIO.36
MASTER-RESET: POWER.2
unnamed: IC1.18 (B1), R3.1
unnamed: IC2.7 (B), R1.1, RS485.4
unnamed: IC2.6 (Z), R2.2, RS485.6
unnamed: IC2.5 (Y), R2.1, RS485.3
unnamed: IC2.8 (A), R1.2, RS485.5
unnamed: JP5.2, PROTOTYPE.2 (A1)
unnamed: JP5.3, PROTOTYPE.3 (A2)
unnamed: JP5.4, PROTOTYPE.4 (A3)
unnamed: JP5.5, PROTOTYPE.5 (A4)
unnamed: JP5.6, PROTOTYPE.6 (A5)
unnamed: JP5.7, PROTOTYPE.7 (A6)
unnamed: JP5.8, PROTOTYPE.8 (A7)
unnamed: JP5.9, PROTOTYPE.9 (A8)
unnamed: JP5.10, PROTOTYPE.10 (GND)
unnamed: JP5.1, PROTOTYPE.1 (DIR)
unnamed: JP4.8, PROTOTYPE.18 (B1)
unnamed: JP4.7, PROTOTYPE.17 (B2)
unnamed: JP4.6, PROTOTYPE.16 (B3)
unnamed: JP4.5, PROTOTYPE.15 (B4)
unnamed: JP4.4, PROTOTYPE.14 (B5)
unnamed: JP4.3, PROTOTYPE.13 (B6)
unnamed: JP4.2, PROTOTYPE.12 (B7)
unnamed: JP4.1, PROTOTYPE.11 (B8)
unnamed: JP4.9, PROTOTYPE.19 (G)
unnamed: JP4.10, PROTOTYPE.20 (VCC)
PIN22: XIO.3
PIN23: XIO.4
PIN24: JP1.7, XIO.5
PIN25: XIO.6
PIN26: JP1.6, XIO.7
PIN27: XIO.8
PIN28: IC1.2 (A1), XIO.9
PIN29: XIO.10
PIN30: JP2.1, R4.1, XIO.11
PIN31: XIO.12
PIN32: JP6.1, XIO.13
PIN33: XIO.14
PIN34: XIO.15
PIN35: XIO.16
PIN36: XIO.17
PIN37: XIO.18
PIN38: XIO.19
PIN39: XIO.20
PIN40: XIO.21
PIN41: XIO.22
PIN42: XIO.23
PIN43: XIO.24
PIN44: XIO.25
PIN45: XIO.26
PIN46: XIO.27
PIN47: XIO.28
PIN48: XIO.29
PIN49: XIO.30
PIN50: XIO.31
PIN51: XIO.32
PWM2: PWML.3
PWM3: PWML.4
PWM5: PWML.6
PWM6: PWML.7
PWM7: PWML.8
PWM8: PWMH.1
PWM9: PWMH.2
PWM11: PWMH.4
PWM12: PWMH.5
PWM13: PWMH.6
RX: PWML.1
RX1: COMMUNICATION.6, IC2.2 (RO)
RX2: COMMUNICATION.4, JP3.2
RX3: COMMUNICATION.2
SCL0: COMMUNICATION.8, JP1.4
SCL1: PWMH.10
SDA0: COMMUNICATION.7, JP1.5
SDA1: PWMH.9
SS0/PWM10: PWMH.3
SS1/PWM4: PWML.5
TX: PWML.2
TX1: COMMUNICATION.5, IC2.3 (DI)
TX2: COMMUNICATION.3, JP3.1
TX3: COMMUNICATION.1
VIN: POWER.7
WS2812DATA: JP1.3, R3.2

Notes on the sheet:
TWCK1
TWD1
IOREF
TWCK0
TWD0
AD1
AD2
AD3
AD4
AD5
AD6
AD0
AREF
AD7
SD-CS
UTXD
URXD
ETH-CS
+5V +3.3V WS2812DATA SCL SDA CLK DIO LDR GND

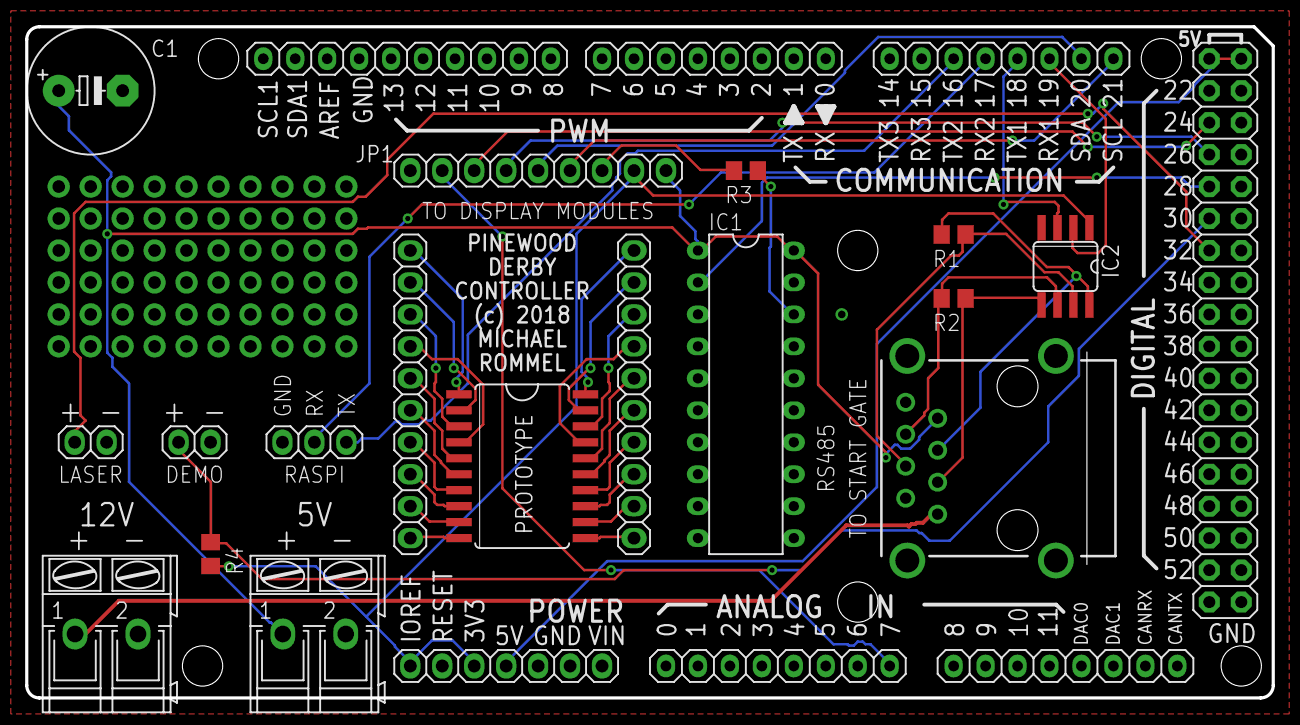
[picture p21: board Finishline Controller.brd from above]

Board: 2 copper layers, 99.1 x 53.3 mm, 24 parts (0 on the bottom side), 43 nets.

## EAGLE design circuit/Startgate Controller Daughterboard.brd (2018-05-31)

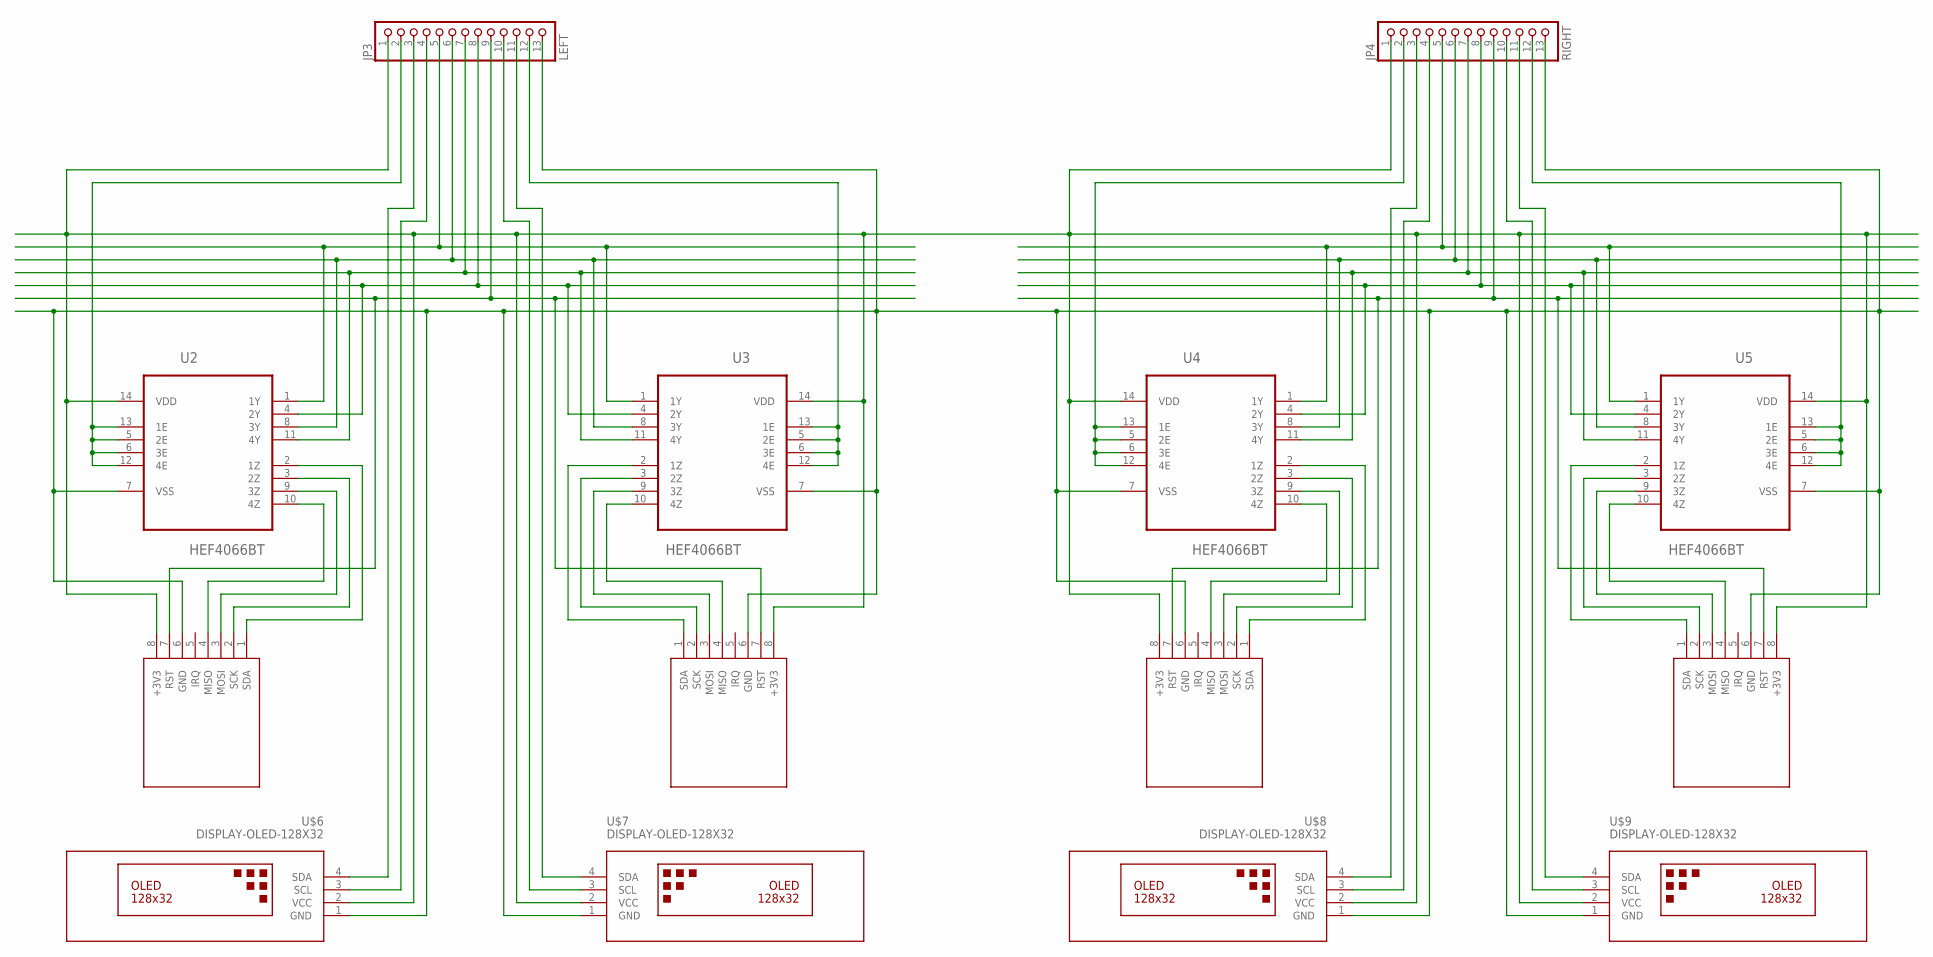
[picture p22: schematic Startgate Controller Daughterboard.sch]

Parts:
JP3: LEFT; 1X13
JP4: RIGHT; 1X13
U2, U3, U4, U5: HEF4066BT; SOIC127P600X175-14N
U$2, U$3, U$4, U$5: RFID-RC522
U$6, U$7, U$8, U$9: DISPLAY-OLED-128X32

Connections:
+3V3: JP3.1, JP4.1, U2.14 (VDD), U3.14 (VDD), U4.14 (VDD), U5.14 (VDD), U$2.8 (+3V3), U$3.8 (+3V3), U$4.8 (+3V3), U$5.8 (+3V3), U$6.2 (VCC), U$7.2 (VCC), U$8.2 (VCC), U$9.2 (VCC)
ENA1: JP3.2, U2.5 (2E), U2.6 (3E), U2.12 (4E), U2.13 (1E)
ENA2: JP3.12, U3.5 (2E), U3.6 (3E), U3.12 (4E), U3.13 (1E)
ENA3: JP4.2, U4.5 (2E), U4.6 (3E), U4.12 (4E), U4.13 (1E)
GND: JP3.13, JP4.13, U2.7 (VSS), U3.7 (VSS), U4.7 (VSS), U5.7 (VSS), U$2.6 (GND), U$3.6 (GND), U$4.6 (GND), U$5.6 (GND), U$6.1 (GND), U$7.1 (GND), U$8.1 (GND), U$9.1 (GND)
MISO: JP4.7, U4.11 (4Y), U5.11 (4Y)
MISO-OUT1: U2.10 (4Z), U$2.4 (MISO)
MISO-OUT2: U3.10 (4Z), U$3.4 (MISO)
MISO-OUT3: U4.10 (4Z), U$4.4 (MISO)
MISO-OUT4: U5.10 (4Z), U$5.4 (MISO)
MOSI: JP4.6, U4.8 (3Y), U5.8 (3Y)
MOSI-OUT1: U2.9 (3Z), U$2.3 (MOSI)
MOSI-OUT2: U3.9 (3Z), U$3.3 (MOSI)
MOSI-OUT3: U4.9 (3Z), U$4.3 (MOSI)
MOSI-OUT4: U5.9 (3Z), U$5.3 (MOSI)
unnamed: JP3.6, U2.8 (3Y), U3.8 (3Y)
unnamed: JP3.5, U2.1 (1Y), U3.1 (1Y)
unnamed: JP3.7, U2.11 (4Y), U3.11 (4Y)
unnamed: JP3.8, U2.4 (2Y), U3.4 (2Y)
unnamed: JP4.12, U5.5 (2E), U5.6 (3E), U5.12 (4E), U5.13 (1E)
RST: JP3.9, JP4.9, U$2.7 (RST), U$3.7 (RST), U$4.7 (RST), U$5.7 (RST)
SCK: JP4.8, U4.4 (2Y), U5.4 (2Y)
SCK-OUT1: U2.3 (2Z), U$2.2 (SCK)
SCK-OUT2: U3.3 (2Z), U$3.2 (SCK)
SCK-OUT3: U4.3 (2Z), U$4.2 (SCK)
SCK-OUT4: U5.3 (2Z), U$5.2 (SCK)
SCL1: JP3.4, U$6.3 (SCL)
SCL2: JP3.10, U$7.3 (SCL)
SCL3: JP4.4, U$8.3 (SCL)
SCL4: JP4.10, U$9.3 (SCL)
SDA1: JP3.3, U$6.4 (SDA)
SDA2: JP3.11, U$7.4 (SDA)
SDA3: JP4.3, U$8.4 (SDA)
SDA4: JP4.11, U$9.4 (SDA)
SS: JP4.5, U4.1 (1Y), U5.1 (1Y)
SS-OUT1: U2.2 (1Z), U$2.1 (SDA)
SS-OUT2: U3.2 (1Z), U$3.1 (SDA)
SS-OUT3: U4.2 (1Z), U$4.1 (SDA)
SS-OUT4: U5.2 (1Z), U$5.1 (SDA)

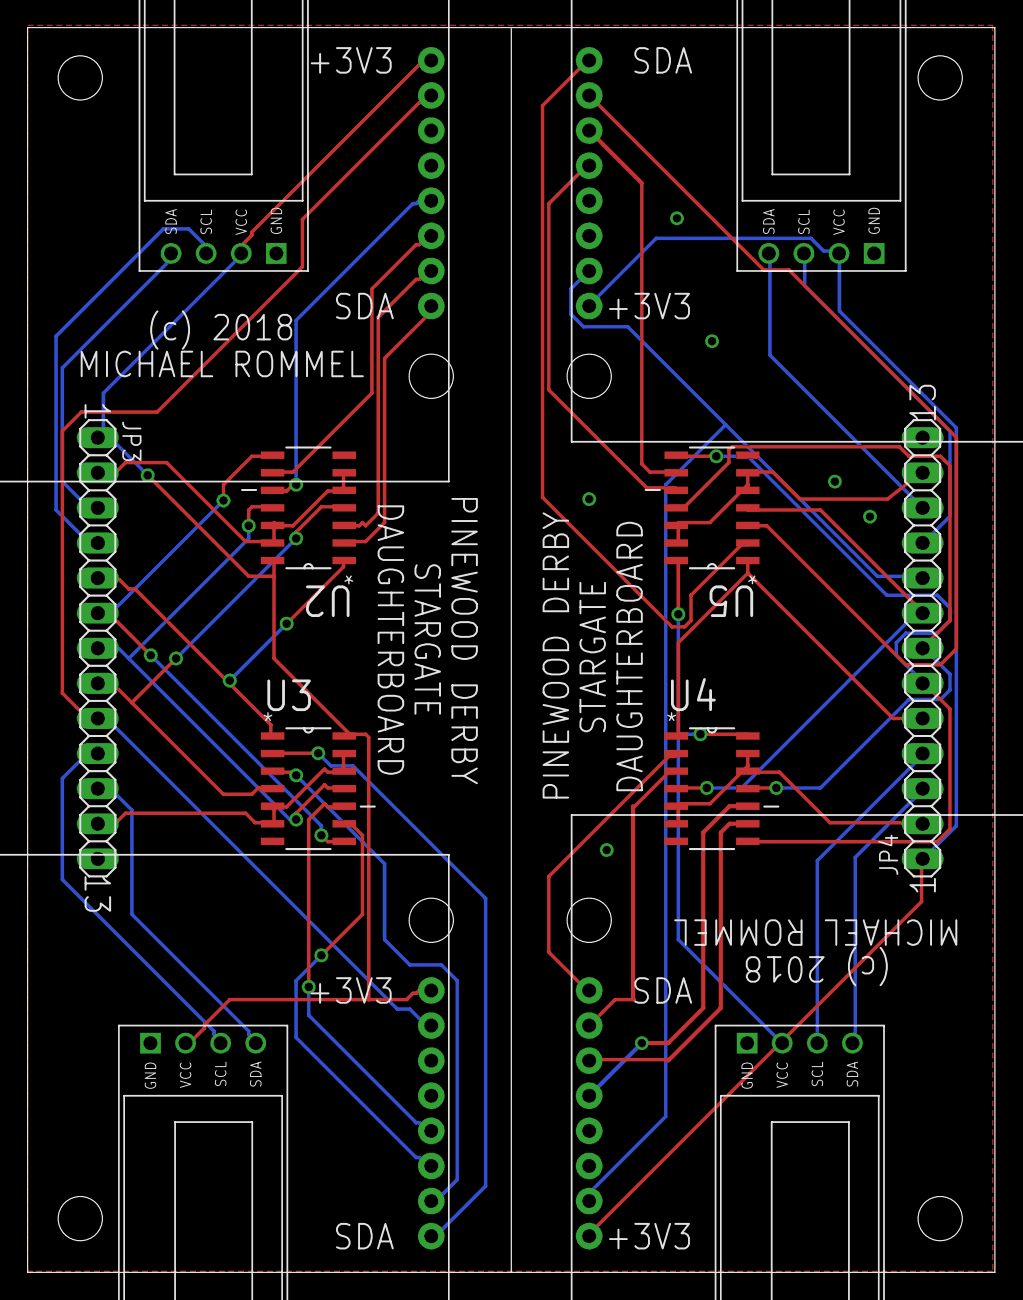
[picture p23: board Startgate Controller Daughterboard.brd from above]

Board: 2 copper layers, 70.0 x 90.1 mm, 14 parts (0 on the bottom side), 39 nets.

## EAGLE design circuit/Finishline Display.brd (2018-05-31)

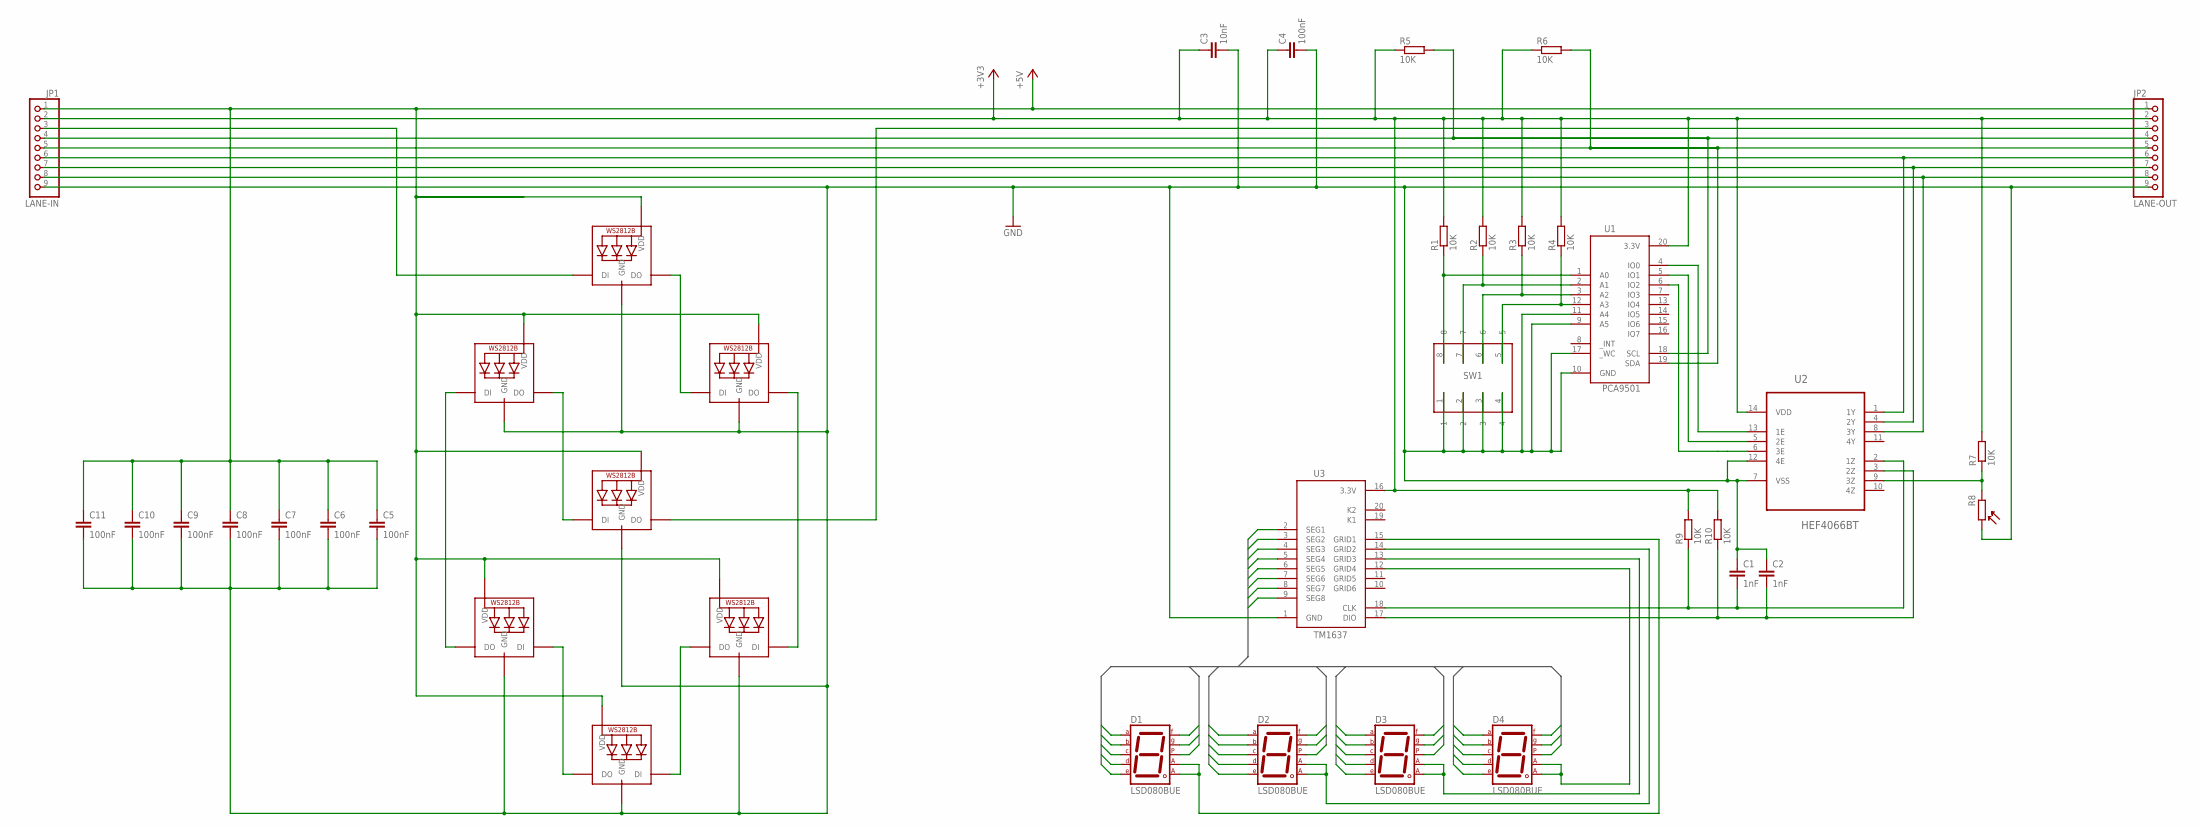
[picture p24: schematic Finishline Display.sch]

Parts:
C1, C2: 1nF; C0805
C3: 10nF; C0805
C4, C5, C6, C7, C8, C9, C10, C11: 100nF; C0805
D1, D2, D3, D4: LSD080BUE; 7SEG-13
JP1: LANE-IN; 1X09
JP2: LANE-OUT; 1X09
LED1, LED2, LED3, LED4, LED5, LED6, LED7: WS2812B5050; WS2812B
R1, R2, R3, R4, R5, R6, R7, R9, R10: 10K; M0805
R8: LDR 10K; 1X02
SW1: 416131160804
U1: PCA9501; SOIC127P1032X265-20N
U2: HEF4066BT; SOIC127P600X175-14N
U3: TM1637; SOIC127P1032X265-20N

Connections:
+3V3: C3.1, C4.1, JP1.2, JP2.2, R1.2, R2.2, R3.2, R4.2, R5.1, R6.1, R7.2, R9.2, R10.2, U1.20 (3.3V), U2.14 (VDD), U3.16 (3.3V)
+5V: C5.1, C6.1, C7.1, C8.1, C9.1, C10.1, C11.1, JP1.1, JP2.1, LED1.1-VDD (VDD), LED2.1-VDD (VDD), LED3.1-VDD (VDD), LED4.1-VDD (VDD), LED5.1-VDD (VDD), LED6.1-VDD (VDD), LED7.1-VDD (VDD)
CLK: JP1.6, JP2.6, U2.1 (1Y)
DIO: JP1.7, JP2.7, U2.4 (2Y)
GND: C1.1, C2.1, C3.2, C4.2, C5.2, C6.2, C7.2, C8.2, C9.2, C10.2, C11.2, JP1.9, JP2.9, LED1.3-GND (GND), LED2.3-GND (GND), LED3.3-GND (GND), LED4.3-GND (GND), LED5.3-GND (GND), LED6.3-GND (GND), LED7.3-GND (GND), R8.2, SW1.1, SW1.2, SW1.3, SW1.4, U1.9 (A5), U1.10 (GND), U1.11 (A4), U1.17 (_WC), U2.7 (VSS), U2.12 (4E), U3.1 (GND)
LDR: JP1.8, JP2.8, U2.8 (3Y)
unnamed: U1.4 (IO0), U2.13 (1E)
unnamed: LED1.2-DOUT (DO), LED2.4-DIN (DI)
unnamed: LED2.2-DOUT (DO), LED3.4-DIN (DI)
unnamed: LED3.2-DOUT (DO), LED4.4-DIN (DI)
unnamed: LED4.2-DOUT (DO), LED5.4-DIN (DI)
unnamed: LED5.2-DOUT (DO), LED6.4-DIN (DI)
unnamed: LED6.2-DOUT (DO), LED7.4-DIN (DI)
unnamed: JP2.3, LED7.2-DOUT (DO)
unnamed: D1.3 (CA1), D1.8 (CA2), U3.15 (GRID1)
unnamed: D2.3 (CA1), D2.8 (CA2), U3.14 (GRID2)
unnamed: D3.3 (CA1), D3.8 (CA2), U3.13 (GRID3)
unnamed: D4.3 (CA1), D4.8 (CA2), U3.12 (GRID4)
unnamed: U1.5 (IO1), U2.5 (2E)
unnamed: R1.1, SW1.8, U1.1 (A0)
unnamed: R2.1, SW1.7, U1.2 (A1)
unnamed: R3.1, SW1.6, U1.3 (A2)
unnamed: R4.1, SW1.5, U1.12 (A3)
unnamed: C1.2, R9.1, U2.2 (1Z), U3.18 (CLK)
unnamed: C2.2, R10.1, U2.3 (2Z), U3.17 (DIO)
unnamed: R7.1, R8.1, U2.9 (3Z)
unnamed: U1.6 (IO2), U2.6 (3E)
SCL: JP1.4, JP2.4, R5.2, U1.18 (SCL)
SDA: JP1.5, JP2.5, R6.2, U1.19 (SDA)
SEG1: D1.7 (A), D2.7 (A), D3.7 (A), D4.7 (A), U3.2 (SEG1)
SEG2: D1.6 (B), D2.6 (B), D3.6 (B), D4.6 (B), U3.3 (SEG2)
SEG3: D1.4 (C), D2.4 (C), D3.4 (C), D4.4 (C), U3.4 (SEG3)
SEG4: D1.2 (D), D2.2 (D), D3.2 (D), D4.2 (D), U3.5 (SEG4)
SEG5: D1.1 (E), D2.1 (E), D3.1 (E), D4.1 (E), U3.6 (SEG5)
SEG6: D1.9 (F), D2.9 (F), D3.9 (F), D4.9 (F), U3.7 (SEG6)
SEG7: D1.10 (G), D2.10 (G), D3.10 (G), D4.10 (G), U3.8 (SEG7)
SEG8: D1.5 (DP), D2.5 (DP), D3.5 (DP), D4.5 (DP), U3.9 (SEG8)
WS2812DATA: JP1.3, LED1.4-DIN (DI)

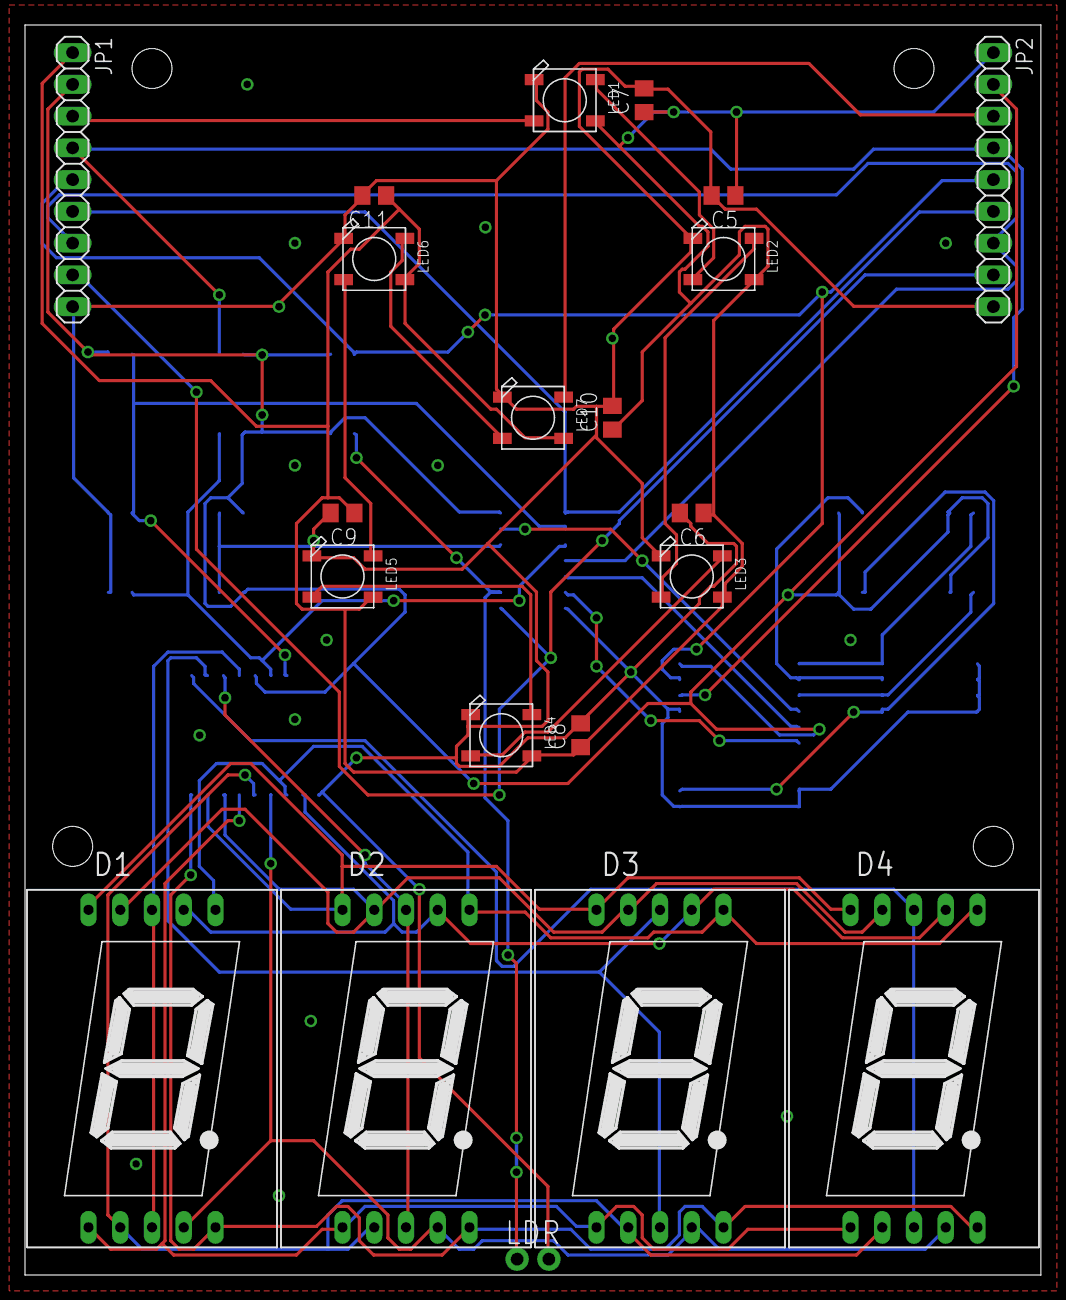
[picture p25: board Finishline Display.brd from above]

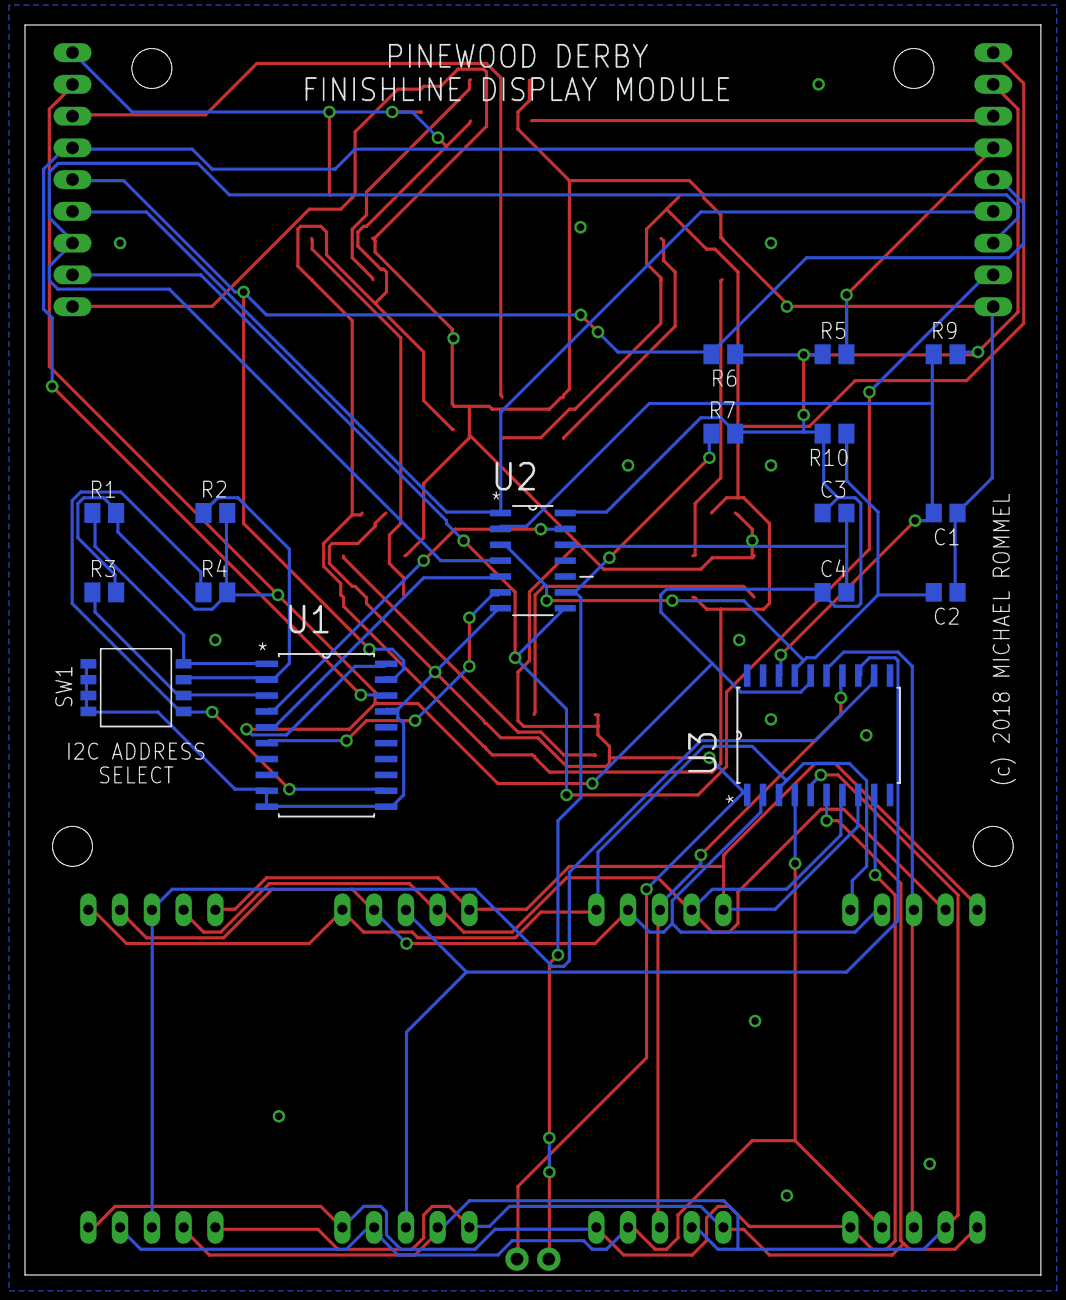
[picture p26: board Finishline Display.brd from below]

Board: 2 copper layers, 81.3 x 100.0 mm, 38 parts (17 on the bottom side), 38 nets.

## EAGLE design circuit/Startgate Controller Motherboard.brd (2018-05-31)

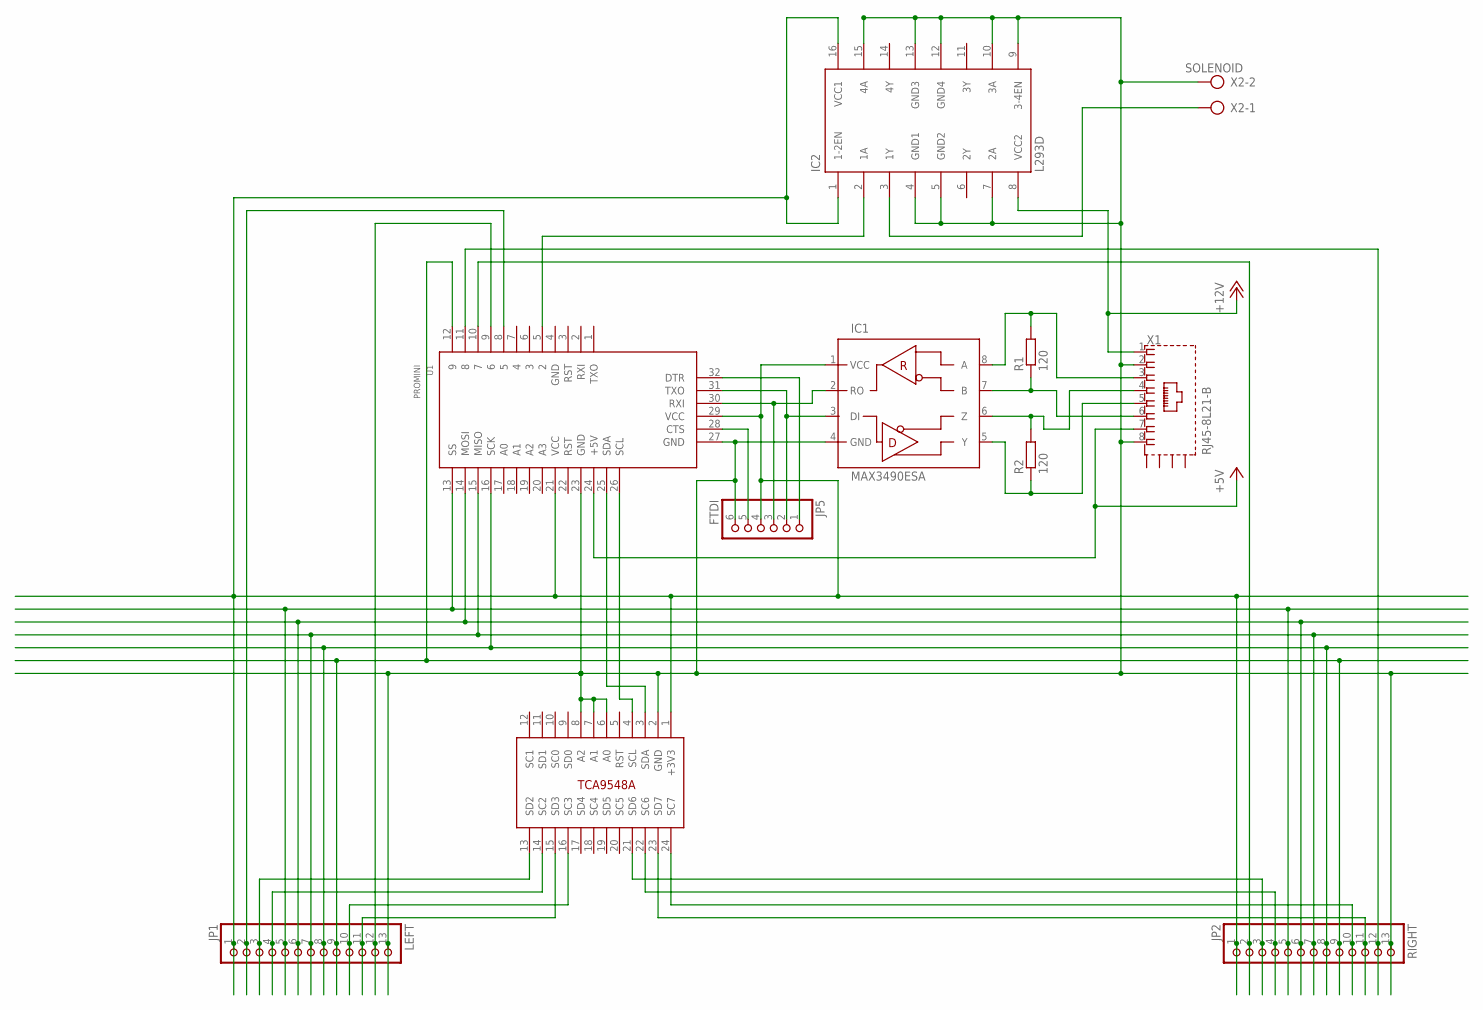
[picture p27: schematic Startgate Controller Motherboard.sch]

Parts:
IC1: MAX3490ESA; SO08
IC2: L293D; DIL16
JP1: LEFT; 1X13
JP2: RIGHT; 1X13
JP5: FTDI; 1X06
R1, R2: 120; R0805
U1: PROMINI; ARDUINOPROMINI
U2: TCA9548A; DIL24
X1: RJ45-8L21-B; RJ45-SHIELD1
X2: SOLENOID; AK300/2

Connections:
+3V3: IC1.1 (VCC), IC2.1 (1-2EN), IC2.16 (VCC1), JP1.1, JP2.1, JP5.4, U1.21 (VCC), U1.29 (VCC), U2.1 (+3V3)
+5V: U1.24 (+5V), X1.7
+12V: IC2.8 (VCC2), X1.1
ENA1: JP1.2, U1.8 (5)
ENA2: JP1.12, U1.9 (6)
ENA3: JP2.2, U1.10 (7)
ENA4: JP2.12, U1.11 (8)
GND: IC1.4 (GND), IC2.4 (GND1), IC2.5 (GND2), IC2.7 (2A), IC2.9 (3-4EN), IC2.10 (3A), IC2.12 (GND4), IC2.13 (GND3), IC2.15 (4A), JP1.13, JP2.13, JP5.6, U1.23 (GND), U1.27 (GND), U2.2 (GND), U2.6 (A0), U2.7 (A1), U2.8 (A2), X1.2, X1.8, X2.2
MISO: JP1.7, JP2.7, U1.15 (MISO)
MOSI: JP1.6, JP2.6, U1.14 (MOSI)
unnamed: IC1.3 (DI), JP5.2, U1.31 (TXO)
unnamed: IC1.2 (RO), JP5.3, U1.30 (RXI)
unnamed: IC1.8 (A), R1.2, X1.3
unnamed: IC1.7 (B), R1.1, X1.6
unnamed: U1.26 (SCL), U2.4 (SCL)
unnamed: U1.25 (SDA), U2.3 (SDA)
unnamed: IC1.5 (Y), R2.1, X1.5
unnamed: IC1.6 (Z), R2.2, X1.4
unnamed: JP5.1, U1.32 (DTR)
unnamed: IC2.2 (1A), U1.5 (2)
unnamed: IC2.3 (1Y), X2.1
unnamed: JP5.5, U1.28 (CTS)
RST: JP1.9, JP2.9, U1.12 (9)
SCK: JP1.8, JP2.8, U1.16 (SCK)
SCL1: JP1.4, U2.14 (SC2)
SCL2: JP1.10, U2.16 (SC3)
SCL3: JP2.4, U2.22 (SC6)
SCL4: JP2.10, U2.24 (SC7)
SDA1: JP1.3, U2.13 (SD2)
SDA2: JP1.11, U2.15 (SD3)
SDA3: JP2.3, U2.21 (SD6)
SDA4: JP2.11, U2.23 (SD7)
SS: JP1.5, JP2.5, U1.13 (SS)

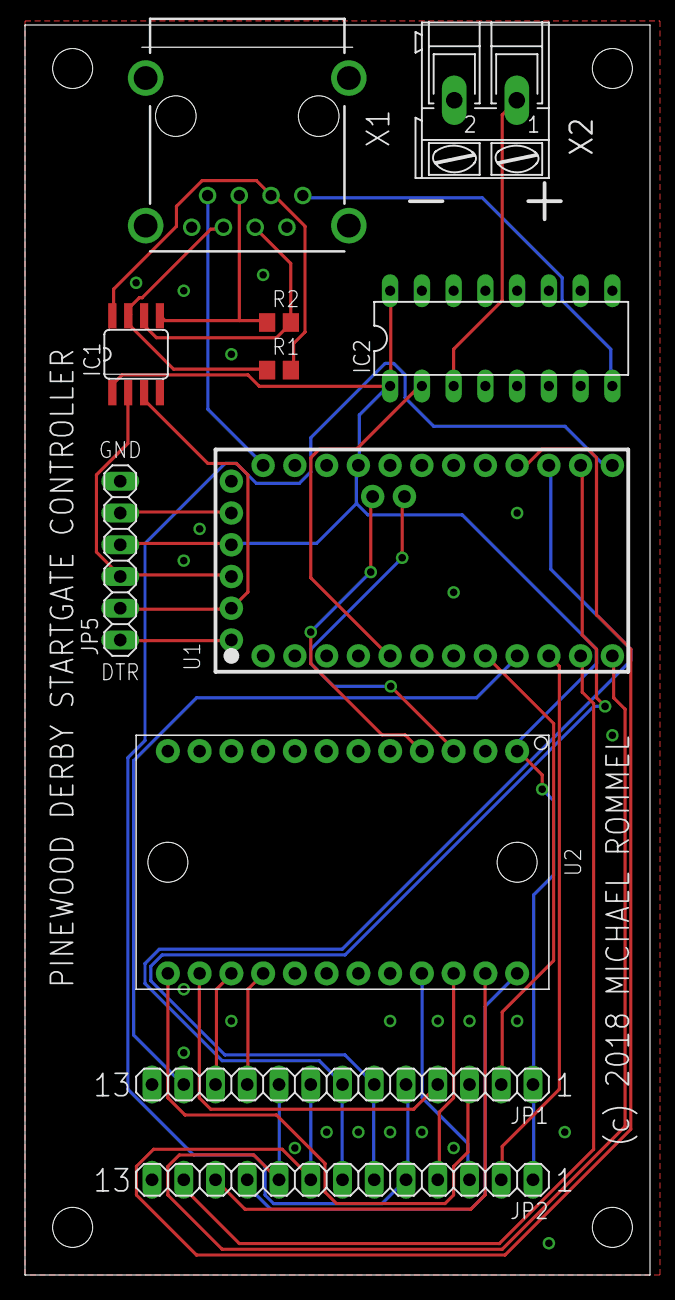
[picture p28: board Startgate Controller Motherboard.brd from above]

Board: 2 copper layers, 50.0 x 100.0 mm, 11 parts (0 on the bottom side), 33 nets.

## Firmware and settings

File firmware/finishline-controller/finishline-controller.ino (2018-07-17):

//
// Racetrack Firmware Finishline Controller
//

#include "FastLED.h"
#include "PWDLaneDisplay.h"
#include "PWDData.h"
#include "PWDProtocol.h"
#include "PWDStatistics.h"
#include "util.h"

#include <malloc.h>
#include <stdlib.h>
#include <stdio.h>

#define FINISHLINE_VERSION "0.1.4"

#define TM1637_DATA 24
#define TM1637_CLOCK 26
#define NEOPIXEL_PIN 28
#define DEMO_PIN 30
#define LASER_PIN 32

#define LDR_PIN A7
#define LDR_THRESHOLD 400

// number of lanes of the track
#define LANES 4
// after this many millis, a car times out
#define MAXRACETIME 8000

// variables needed to display free memory
extern char _end;
extern "C" char *sbrk(int i);

// the array of all RGB LEDs needs to be global here, as it is shared across
// all lane displays
CRGB leds[LANES*7];

// instantiate the <n> lanes
PWDLaneDisplay laneDisplay[LANES] = {
  PWDLaneDisplay( 0, TM1637_CLOCK, TM1637_DATA, leds, CRGB( 255, 255,   0) ),  
  PWDLaneDisplay( 1, TM1637_CLOCK, TM1637_DATA, leds, CRGB( 255, 255,   0) ),  
  PWDLaneDisplay( 2, TM1637_CLOCK, TM1637_DATA, leds, CRGB( 255, 255,   0) ),  
  PWDLaneDisplay( 3, TM1637_CLOCK, TM1637_DATA, leds, CRGB( 255, 255,   0) ),  
};

// instantiate three serial communication channels
// channel to bridge
PWDProtocol combr( Serial, 57600 );
// define acceptable commands for use in begin()
uint8_t combr_whitelist[4][8] = {
  { // IDLE
    PWDProtocol::CODE_ACK, PWDProtocol::CODE_INIT,
    PWDProtocol::CODE_SETUP
  },
  { // HEATSETUP
    PWDProtocol::CODE_ACK, PWDProtocol::CODE_INIT,
    PWDProtocol::CODE_GO, PWDProtocol::CODE_SETUP
  },
  { // RACING
    PWDProtocol::CODE_ACK
  },
  { // TRACKSETUP
    PWDProtocol::CODE_ACK, PWDProtocol::CODE_SETUP
  }
};
// channel to Raspberry Pi
PWDProtocol compi( Serial2, 57600 );
// define acceptable commands for use in begin()
uint8_t compi_whitelist[4][8] = {
  { // IDLE
    PWDProtocol::CODE_ACK
  },
  { // HEATSETUP
    PWDProtocol::CODE_ACK, PWDProtocol::CODE_GO
  },
  { // RACING
  },
  { // TRACKSETUP
  }
};
// channel to Startgate
PWDProtocol comsg( Serial1, 19200 );
// define acceptable commands for use in begin()
uint8_t comsg_whitelist[4][8] = {
  { // IDLE
    PWDProtocol::CODE_ACK, PWDProtocol::CODE_DETECT
  },
  { // HEATSETUP
    PWDProtocol::CODE_ACK, PWDProtocol::CODE_DETECT, 
    PWDProtocol::CODE_COMPLETE
  },
  { // RACING
    PWDProtocol::CODE_ACK
  },
  { // TRACKSETUP
  }
};

// global main data structure for a heat
// this is populated by the bridge
PWDHeat heat;
// 4 lanes
PWDLane lane[LANES];
// 4 character arrays, 14 characters plus \0
char rfid[LANES][15];
// 4 owners, 15 characters plus \0
char owner[LANES][16];

// data structure for the heat setup phase
// this is populated when the startgate detects cars
PWDHeat setupHeat;
// 4 lanes
PWDLane setupLane[LANES];
// 4 character arrays, 14 characters plus \0
char setupRfid[LANES][15];
// 4 owners, 15 characters plus \0
char setupOwner[LANES][16];

// instance for loop stats
PWDStatistics loopStats( SerialUSB );

// flag, that a state change happened and the new
// state needs the initialisation routine
bool stateInitNeeded;

// variables for race timings
unsigned long elapsed;
unsigned long start;

// bit array indicating if the car in this lane has finished  
// LSB = lane 0, MSB = lane 4 (or more...)
int lane_status;
// counter, how many cars have finished thiÂs heat
int finishers;
// number of lanes to finish (some may be empty in a heat)
int expectedFinishers;
// rank contains the lane numbers in the order they finish
int rank[LANES] = {0, 0, 0, 0};
// place contains the finishing place in lane order
int place[LANES] = {0, 0, 0, 0};
// inidcator that the big displays need updating
bool update_rank;

// variables for demo mode
unsigned long emitterWatchdog;


//
// Helper functions that are necessary for the main loop
//

// lane display selection we have to unselect all lanes first,
// otherwise two lanes might temporarily end up both selected.
void select_laneDisplay( int l ) {
  for( int n=0; n<LANES; n++ ) {
    // n == l equals false for all lanes other than the desired one
    laneDisplay[n].select( n == l );
  }
  laneDisplay[l].select( true );
}

// routine to clear all displays of a lane, small and big
void clearDisplays() {
  for( int n=0; n<LANES; n++ ) {
    select_laneDisplay( n );
    laneDisplay[n].showNumber( 0 );
    laneDisplay[n].setBigDigit( PWDLaneDisplay::DIGIT_OFF );
  }
  // unselect last lane to achieve a stable state for the LDR line
  laneDisplay[3].select( false );
  FastLED.show();
}

// get the number of participants in this heat, lanes may be empty
uint8_t getExpectedFinishers() {
  uint8_t ef = 0;
  for( int i=0; i<4; i++ ) {
    if( strlen(heat.lane[i]->rfid) > 0 ) ef++;
  }
  return ef;
}

// routine that gets called once per loop when the race is running
// returnes true, if at leat one more car finished
bool checkOrSetFinishers( uint8_t setFinishLane = 0xFF ) {
  bool bigDisplayUpdate = false;
  bool oneMore = false;
  int ldr = 0;
  for( int n=0; n<4; n++) {
    // if the lane has not finished and should have a car on it
    // loop iteration, then update the millis display
    if( ! (lane_status & (1 << n)) && (strlen(heat.lane[n]->rfid) > 0) ) {
      if( elapsed >= MAXRACETIME ) {
        // this lane has not finished but exceeded the maximum race time
        // force finishing of this lane
        setFinishLane = n;
      }
      // select lane chip
      select_laneDisplay( n );
      laneDisplay[n].showNumber( elapsed );
      if( setFinishLane == 0xFF ) {
        // we shall check the LDR
        ldr = analogRead( A7 );
        //SerialUSB.print( "LDR " );
        //SerialUSB.print( n );
        //SerialUSB.print( " = " );
        //SerialUSB.println( ldr );
      }
      if( ( ldr > LDR_THRESHOLD ) || ( setFinishLane == n ) ){
        SerialUSB.print( "Laser break on lane " );
        if( setFinishLane != 0xFF ) SerialUSB.print( "(simulated) ");
        SerialUSB.println( n );
        // detected laser beam break
        // TODO: add array for multiple consecutive breaks from original sketch.
        //       may actually not be needed as the loop is around 18ms
        // set bit for this lane
        lane_status = lane_status | (1 << n);
        // increase number of finishers (1-4)
        finishers++;
        // remember the lane for the n-th finisher
        rank[finishers-1] = n;
        // remember the place for this lane
        place[n] = finishers;
        // record time
        heat.lane[n]->time = elapsed;
        // remember to update the big displays
        bigDisplayUpdate = true; 
        // set the raw data now, update the display later for all at once
        laneDisplay[n].setBigDigit( place[n] );
        // remember return code that one car finished
        oneMore = true;
      }
    }
  }
  // unselect last lane to achieve a stable state for the LDR line
  laneDisplay[3].select( false );
  // only push updates to the LEDs, if necessary, as it blocks serial interrupts
  if( bigDisplayUpdate ) {
    SerialUSB.println( "Updating big displays" );
    FastLED.show();
    bigDisplayUpdate = false;
  }
  return oneMore;
}


// displays the measured light level of the light dependend resistors  
void showLaserLevel() {
  for( int n=0; n<4; n++) {
    // select lane chip
    select_laneDisplay( n );
    // small delay to have the LDRs settle
    delay(10);
    // we shall check the LDR
    int ldr = analogRead( A7 ) / 10;
    laneDisplay[n].showNumber( ldr );
    heat.lane[n]->laser = ldr;
  }
  laneDisplay[3].select( false );
}


// resets all the counters for a heat run
void resetHeat() {
  SerialUSB.println( "resetHeat()" );
  // switch on the lasers
  digitalWrite( LASER_PIN, HIGH );
  // blank the displays
  clearDisplays();
  // remember preliminary start time
  start = millis();
  // reset elapsed var
  elapsed = 0;
  // following should be taken care of in the idle init
  // reset race times
  //for( int i=0; i<4; i++ ) {
  //  heat.lane[i]->time = 0;
  //}
  // no lane has finished
  lane_status = 0;
  // number of cars which finished is zero
  finishers = 0;
  // get the number of participants
  expectedFinishers = getExpectedFinishers();
}

// clears any information from previous runs
void clearHeat( PWDHeat* heat ) {
  heat->state = PWDProtocol::STATE_IDLE;
  heat->status = PWDProtocol::STATUS_OK;
  heat->heatno = 0;
  for( int i=0; i<4; i++ ) {
    *heat->lane[i]->rfid = '\0';
    *heat->lane[i]->owner = '\0';
    heat->lane[i]->modelno = 0;
    heat->lane[i]->serno = 0;
    heat->lane[i]->time = 0;
  }
}

// link the data structures together
void initStructures( void ) {
  // initialize the lane and heat structure for the race heat
  // this should be now a fixed data structure in globals
  for( int i=0; i<4; i++ ) {
    lane[i].rfid = &rfid[i][0];
    lane[i].owner = &owner[i][0];
    lane[i].time = 0;
    heat.lane[i] = &lane[i];
  }
  heat.state = PWDProtocol::STATE_IDLE;
  heat.status = PWDProtocol::STATUS_OK;
  heat.heatno = 0;

  // initialize the lane and heat structure while setting up
  // this should be now a fixed data structure in globals
  for( int i=0; i<4; i++ ) {
    setupLane[i].rfid = &setupRfid[i][0];
    setupLane[i].owner = &setupOwner[i][0];
    setupLane[i].time = 0;
    setupHeat.lane[i] = &setupLane[i];
  }
  setupHeat.state = PWDProtocol::STATE_IDLE;
  setupHeat.status = PWDProtocol::STATUS_OK;
  setupHeat.heatno = 0;
}


// for debugging echo the current heat structure to the Serial port
void dumpHeat( PWDHeat* heat ) {
  SerialUSB.print( F("Heat: ") );
  SerialUSB.println( heat->heatno );
  SerialUSB.print( F("State: ") );
  SerialUSB.println( heat->state );
  SerialUSB.print( F("Status: ") );
  SerialUSB.println( heat->status );
  for( int i=0; i<LANES; i++ ) {
    SerialUSB.print( F("Lane: ") );
    SerialUSB.println( i );
    SerialUSB.print( F("  RFID: ") );
    SerialUSB.println( heat->lane[i]->rfid );
    SerialUSB.print( F("  Owner: ") );
    SerialUSB.println( heat->lane[i]->owner );
    SerialUSB.print( F("  Model No.: ") );
    SerialUSB.println( heat->lane[i]->modelno );
    SerialUSB.print( F("  Serial No.: ") );
    SerialUSB.println( heat->lane[i]->serno );
    SerialUSB.print( F("  Time: ") );
    SerialUSB.println( heat->lane[i]->time );
  }
  //combr.sendCompleteOrProgress( PWDProtocol::CODE_COMPLETE, &heat );
  //combr.sendCompleteOrProgress( PWDProtocol::CODE_COMPLETE, &setupHeat );
}


//
// Setup all needed peripherals
//
void setup() {

  pinMode( LED_PIN, OUTPUT );

  // initialize all communication channels
  combr.begin( combr_whitelist );
  compi.begin( compi_whitelist );
  comsg.begin( comsg_whitelist );

  SerialUSB.begin( 57600 );

  // set up the linked data structures for 
  // heat and setup status
  initStructures();

  // set all pin modes
  pinMode( DEMO_PIN, INPUT_PULLUP );
  pinMode( LASER_PIN, OUTPUT );
  pinMode( LDR_PIN, INPUT );
  pinMode( NEOPIXEL_PIN, OUTPUT );

  // initialize the LED library (strip type, pin number, variable,
  // number of LEDs
  FastLED.addLeds<NEOPIXEL, NEOPIXEL_PIN>(leds, LANES * 7);

  // clear displays
  for( int n=0; n<LANES; n++ ) {
    select_laneDisplay( n );
    laneDisplay[n].begin();
    laneDisplay[n].showNumber( n );
    laneDisplay[n].setBigDigit( PWDLaneDisplay::DIGIT_OFF );
  }
  FastLED.show();

  // reset statistics
  loopStats.reset();

  // for demo mode, we need a random timer when to fire new
  // messages 
  emitterWatchdog = 0;
  randomSeed( analogRead(A9) );

  // visually signal that SerialUSB should be ready now
  Util::blink( FAST );
  Serial.print( F("{\"name\": \"Pinewood Derby Finishline\", \"version\": \"") );
  Serial.print( FINISHLINE_VERSION );
  Serial.println( F("\"}") );
  Util::ShowMemory( SerialUSB, &_end, sbrk(0) );
  //SerialUSB.println( F("Finished setup()") );

}

//
// main loop
//
void loop() {

  // remember current time and reset the flag for updating the 
  // big displays
  elapsed = (millis() - start);
  update_rank = false;
  // read demo switch
  int demo = digitalRead( DEMO_PIN );

  switch( heat.state ) {

		case PWDProtocol::STATE_IDLE:
      {
        if( stateInitNeeded ) {
          // reset flag
          stateInitNeeded = false;
          // do not change the displays, audience should be able
          // to view the race results!
          // clear all data structures from a previous heat
          clearHeat( &heat );
          clearHeat( &setupHeat );
          // state changed
          SerialUSB.print("State changed to: " );
          SerialUSB.println( heat.state );
        }
        // check connection to startgate
        if( comsg.available() ) {
          // read and process the serial command
          bool res = comsg.receiveCommand( &setupHeat );
          if( res ) {
            // startgate will not change the state
            // in this state we will only receive detect
            // messages from the startgate. res will
            // tell us if we need to emit one to the 
            // bridge
            for( int i=0; i<LANES; i++ ) {
              if( *setupHeat.lane[i]->rfid != '\0' ) {
                combr.sendCarDetection( i, setupHeat.lane[i]->rfid );
                compi.sendCarDetection( i, setupHeat.lane[i]->rfid );
              }
            }
          }
        }
        // check serial connection to bridge
        if( combr.available() ) {
          // read and process the serial command
          bool res = combr.receiveCommand( &heat );
          if( res ) {
            // state changed
            SerialUSB.print("bridge requested state change to: " );
            SerialUSB.println( heat.state );
            // cancel watchdog
            emitterWatchdog = 0;
            stateInitNeeded = true;
          }
        }
        // check if we are in demo mode, if so
        // generate random detect messages
        if( demo ) {
          if( emitterWatchdog > 1 ) {
            // the watchdog has been set
            if ( millis() > emitterWatchdog ) {
              // it has fired
              uint8_t detectlane = Util::createRandomCarDetection( &setupHeat );
              combr.sendCarDetection( detectlane, setupHeat.lane[detectlane]->rfid );
              compi.sendCarDetection( detectlane, setupHeat.lane[detectlane]->rfid );
              // renew watchdog
              emitterWatchdog = millis() + random(30000, 60000);
            }
          } else {
            // shall now set the watchdog
            emitterWatchdog = millis() + random(4000, 8000);
          } 
        } else {
          // production code
          // TODO - unsure if there is anything left to do here besides some fancy
          // LED animation :-)
        }
        break;
      }

    case PWDProtocol::STATE_HEATSETUP:
      {
        if( stateInitNeeded ) {
          // reset flag
          stateInitNeeded = false;
          // blank the displays
          clearDisplays();
          // set correct heat status 
          heat.status =  PWDProtocol::STATUS_OK;
          // send the setup to the startgate
          comsg.sendSkinnyInit( &heat );
          // state changed
          SerialUSB.print("State changed to: " );
          SerialUSB.println( heat.state );
        }
        // check connection to startgate
        if( comsg.available() ) {
          // read and process the serial command
          bool res = comsg.receiveCommand( &setupHeat );
          if( res ) {
            // startgate will not change the state in this state we will
            // receive detect messages or complete messages from the startgate.
            // res will tell us if we need to emit one to the bridge
            //dumpHeat( &setupHeat );
            // if the status is complete
            if( setupHeat.status == PWDProtocol::STATUS_SETUPCOMPLETE ) {
              // send complete message
              heat.status = PWDProtocol::STATUS_SETUPCOMPLETE;
              combr.sendCompleteOrProgress( PWDProtocol::CODE_COMPLETE, &heat );
              compi.sendCompleteOrProgress( PWDProtocol::CODE_COMPLETE, &heat );
            } else {
              // forward detect message
              for( int i=0; i<LANES; i++ ) {
                if( *setupHeat.lane[i]->rfid != '\0' ) {
                  SerialUSB.print( F("car detected on lane ") );
                  SerialUSB.println( i );
                  // need to amend information, since we got it "skinny"
                  // change empty information to dummies to keep the Android
                  // app happy...
                  if( strlen( setupHeat.lane[i]->owner ) == 0 ) {
                    if( strlen( heat.lane[i]->owner ) != 0 ) {
                      // real heat has valid info
                      strncpy( setupHeat.lane[i]->owner, heat.lane[i]->owner, 15 );
                    } else {
                      strncpy( setupHeat.lane[i]->owner, "dummy\0", 6 );
                    }
                  }
                  if( setupHeat.lane[i]->modelno == 0 ) {
                    if( heat.lane[i]->modelno != 0 ) {
                      // real heat has valid info
                      setupHeat.lane[i]->modelno = heat.lane[i]->modelno;
                    } else {
                      setupHeat.lane[i]->modelno = 99999;
                    }
                  }
                  if( setupHeat.lane[i]->serno == 0 ) {
                    if( heat.lane[i]->serno != 0 ) {
                      // real heat has valid info
                      setupHeat.lane[i]->serno = heat.lane[i]->serno;
                    } else {
                      setupHeat.lane[i]->serno = 999;
                    }
                  }
                  combr.sendCarDetection( setupHeat.heatno, i, setupHeat.lane[i], 
                      (setupHeat.status == PWDProtocol::STATUS_WRONGLANE) ? true : false );
                  compi.sendCarDetection( setupHeat.heatno, i, setupHeat.lane[i], 
                      (setupHeat.status == PWDProtocol::STATUS_WRONGLANE) ? true : false );
                }
              }
            }
          }
        }
        // check serial connection to bridge
        if( combr.available() ) {
          // read and process the serial command
          bool res = combr.receiveCommand( &heat );
          if( res ) {
            // state change
            SerialUSB.print("bridge requested state change to: " );
            SerialUSB.println( heat.state );
            stateInitNeeded = true;
            // cancel watchdog
            emitterWatchdog = 0;
          }
        }
        // check if we are in demo mode, if so
        // generate random detect messages
        if( demo ) {
          if( emitterWatchdog > 1 ) {
            // the watchdog has been set
            if ( millis() > emitterWatchdog ) {
              // it has fired
              SerialUSB.println( "Crafting random detect message" );
              uint8_t detectlane = Util::createRandomCarDetection( &heat, &setupHeat );
              if ( detectlane == 4 ) {
                // this means, all cars are right on the track
                SerialUSB.println( "Setup correct" );
                heat.status = PWDProtocol::STATUS_SETUPCOMPLETE;
                combr.sendCompleteOrProgress( PWDProtocol::CODE_COMPLETE, &heat );
                compi.sendCompleteOrProgress( PWDProtocol::CODE_COMPLETE, &heat );
              } else {
                bool wronglane = strncmp( setupHeat.lane[detectlane]->rfid, heat.lane[detectlane]->rfid, 14 );
                SerialUSB.print( "wronglane is ");
                SerialUSB.print( wronglane );
                SerialUSB.print( " for lane ");
                SerialUSB.println( detectlane );
                combr.sendCarDetection(heat.heatno, detectlane, setupHeat.lane[detectlane], wronglane );
                SerialUSB.println( "Showing current heat structures" );
              }
              //dumpHeat();
              // renew watchdog
              emitterWatchdog = millis() + random(3000, 8000);
            }
          } else {
            // shall now set the watchdog
            emitterWatchdog = millis() + random(1000, 4000);
            SerialUSB.print( "Setting watchdog to: " );
            SerialUSB.println( emitterWatchdog );
          } 
        } else {
          // production code
          // TODO - unsure if there is anything left to do here besides some fancy
          // LED animation :-)
        }
        break;
      }
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

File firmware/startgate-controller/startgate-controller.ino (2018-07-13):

//
// Racetrack Firmware Startgate Controller
//

#include "PWDSkinnyData.h"
#include "PWDSkinnyProtocol.h"
#include "PWDStatistics.h"
#include "PWDStartGateDisplayReader.h"
#include "util.h"

#include <Arduino.h>

#include <stdlib.h>
#include <stdio.h>

#define STARTGATE_VERSION "0.1.0"

#define STARTGATE_PIN 45
#define SOLENOID_OPENTIME 1500

#define LANES 4

// variables needed to display free memory
extern char _end;
extern "C" char *sbrk(int i);

// instantiate serial communication channels
// channel to finish line
PWDProtocol comfl( Serial1, 19200 );
// define acceptable commands for use in begin()
uint8_t comfl_whitelist[4][8] = {
  { // IDLE
    PWDProtocol::CODE_ACK, PWDProtocol::CODE_INIT
  },
  { // HEATSETUP
    PWDProtocol::CODE_ACK, PWDProtocol::CODE_INIT,
    PWDProtocol::CODE_GO
  },
  { // RACING
    PWDProtocol::CODE_ACK
  },
  { // TRACKSETUP
    // not needed for startgate
  }
};

// global main data structure for a heat
// this is populated by the bridge
PWDHeat heat;
// 4 lanes
PWDLane lane[LANES];
// 4 character arrays, 14 characters plus \0
char rfid[LANES][15];
// 4 owners, 15 characters plus \0
char owner[LANES][16];

// data structure for the heat setup phase
// this is populated when the startgate detects cars
PWDHeat setupHeat;
// 4 lanes
PWDLane setupLane[LANES];
// 4 character arrays, 14 characters plus \0
char setupRfid[LANES][15];
// 4 owners, 15 characters plus \0
char setupOwner[LANES][16];

// instance for loop stats
PWDStatistics loopStats( Serial );

// array of ss pins for selecting one RFID reader
const uint8_t readerSelectPin[LANES] = {
  42, 41, 44, 43
};

// instance of OLED displays
PWDStartGateDisplayReader oledreader[LANES] = {
//PWDStartGateDisplayReader oledreader[1] = {
  PWDStartGateDisplayReader( 6, true, readerSelectPin, 0 ),
  PWDStartGateDisplayReader( 7, false, readerSelectPin, 1 ),
  PWDStartGateDisplayReader( 2, true, readerSelectPin, 2 ),
  PWDStartGateDisplayReader( 3, false, readerSelectPin, 3 )
};

// flag, that a state change happened and the new
// state needs the initialisation routine
bool stateInitNeeded;
// flag, if solenoid has been opened
bool gateOpen;
// timer for some operations
unsigned long emitterWatchdog;
// index, which lane shall be checked next for new RFIDs
uint8_t nextRFIDCheck;

//
// Helper functions that are necessary for the main loop
//

// shows free ram on a pro mini or mega
int freeRam() {
    extern int __heap_start, *__brkval;
    int v;
    return (int) &v - (__brkval == 0 ?
            (int) &__heap_start :
            (int) __brkval);
}


// resets all the counters for a heat run
void initializeRace() {
  Serial.println( "initializeRace()" );
  // set correct heat status 
  heat.status =  PWDProtocol::STATUS_HEATINPROGRESS;
}

// clears any information from previous runs
void clearHeat( PWDHeat* heat ) {
  heat->state = PWDProtocol::STATE_IDLE;
  heat->status = PWDProtocol::STATUS_OK;
  heat->heatno = 0;
  for( int i=0; i<4; i++ ) {
    *heat->lane[i]->rfid = '\0';
    *heat->lane[i]->owner = '\0';
  }
}


// link the data structures together
void initStructures( void ) {
  // initialize the lane and heat structure for the race heat
  // this should be now a fixed data structure in globals
  for( int i=0; i<4; i++ ) {
    lane[i].rfid = &rfid[i][0];
    lane[i].owner = &owner[i][0];
    heat.lane[i] = &lane[i];
  }
  heat.state = PWDProtocol::STATE_IDLE;
  heat.status = PWDProtocol::STATUS_OK;
  heat.heatno = 0;

  // initialize the lane and heat structure while setting up
  // this should be now a fixed data structure in globals
  for( int i=0; i<4; i++ ) {
    setupLane[i].rfid = &setupRfid[i][0];
    setupLane[i].owner = &setupOwner[i][0];
    setupHeat.lane[i] = &setupLane[i];
  }
  setupHeat.state = PWDProtocol::STATE_IDLE;
  setupHeat.status = PWDProtocol::STATUS_OK;
  setupHeat.heatno = 0;
}


// for debugging echo the current heat structure to the Serial port
void dumpHeat() {
  comfl.sendCompleteOrProgress( PWDProtocol::CODE_COMPLETE, &heat );
  comfl.sendCompleteOrProgress( PWDProtocol::CODE_COMPLETE, &setupHeat );
}


//
// Setup all needed peripherals
//
void setup() {

  // initialize all communication channels
  comfl.begin( comfl_whitelist );

  Serial.begin( 57600 );

  // set up the linked data structures for 
  // heat and setup status
  initStructures();

  // set all pin modes
  pinMode( STARTGATE_PIN, OUTPUT );
  for( int i=0; i<LANES; i++ ) {
    pinMode( readerSelectPin[i], OUTPUT );
  }

  // init the I2C and SPI busses
  Wire.begin();
	SPI.begin();

  // initialize the OLED displays
  oledreader[0].begin();
  oledreader[1].begin();
  oledreader[2].begin();
  oledreader[3].begin();

  // reset statistics
  loopStats.reset();

  // take turns in checking each lane
  nextRFIDCheck = 0;
  // for demo mode, we need a random timer when to fire new
  // messages 
  emitterWatchdog = 0;
  randomSeed( analogRead(A3) );

  // visually signal that Serial should be ready now
  Util::blink( FAST );
  Serial.print( F("\n\nPinewood Derby Startgate Version ") );
  Serial.println( STARTGATE_VERSION );
  Serial.println();
  Serial.print( F("Free RAM: ") );
  Serial.println( freeRam() );
  //Serial.println( F("Finished setup()") );

}
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

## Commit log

2018-05-16 adds eagle files for the electronics
    The schematics and board layouts have been created in Eagle.
    [Finishline Display.brd, Finishline Display.sch]
2018-05-21 changes circuit to include capacitors
    This change adds resistors and capacitors to the LED driver chip
    as well as individual caps to each WS2812 LED.
    [Finishline Display.brd, Finishline Display.sch]
2018-05-23 add Controller brd+sch, fix Display LDR line
    An additional board for the controller was added as a Due shield.
    The LDR was hooked up to a digital pin, has been changed to use
    a separate line which gets patched through the 4066.
    [Finishline Controller.brd, Finishline Controller.sch, Finishline Display.brd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]
2018-05-24 add preliminary Due shield
    The Due shield has been populated with all components to drive the
    display as well as communicate with the start gate electronics.
    A prototyping area with THT and SMD pads has been added as well.
    [Finishline Controller.brd, Finishline Controller.sch]
2018-05-24 add PDF documents for schematics and board
2018-05-24 add mounting holes to the Finishline Display board
    New PDFs have been added for the display.
    [Finishline Controller.brd, Finishline Controller.sch, Finishline Display.brd]
2018-05-26 finalize display module and controller shield
    Display Module: Reordered the WS2813 LEDs to be consistent with normal
    7-segment LED numbers (a-g). Changed schematics to be in the same
    orientation as the board in top view. Re-adds the capacitors for the
    WS2812 LEDs and the LDR line, which inadvertently got lost in the last
    commit. Added silk screen.
    Controller Shield: Added large electrolyte capacitor to buffer for the
    WS2812 LEDs. Added a series resistor for the WS2812 data line. Added
    silk screen and corrected wrong pinout of the I2C and serial header.
    [Finishline Controller.brd, Finishline Controller.sch, Finishline Display.brd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]
2018-05-26 reduce the PCB size of the controller shield to max. 10cm
    [Finishline Controller.brd]
2018-05-26 change the pin assignment for LDR and WS2812DATA
    This uses a high power pin for the LED data and a normal analog pin for
    the LDR line.
    [Finishline Controller.brd, Finishline Controller.sch]
2018-05-28 add the circuitry for the startgate main- and daughterboards
    The main startgate controller has been split up into main board
    and daughterboards, to make it easier to send them to the board house.
    The two daughterboards should be identical, so the next iteration will
    skip one.
    [Startgate Controller-Daughterboard.brd, Startgate Controller-Daughterboard.sch, Startgate Controller-Mainboard.brd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]
2018-05-29 correct some schematics mistakes and add gerber files
    A demo mode button was added to the controller, the layout of the
    controller shield as well as the startgate displays were changed.
    [Finishline Controller.brd, Finishline Controller.sch, Finishline Display.brd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]
2018-05-31 create the final schematics and boards
    Some schematics errors have been corrected. Another connector for
    the laser diodes of the Finishing Gate has been added. The
    connectors to the daughterboards have been rotated, so that the
    cabling will run mostly straight.
    All gerber files have been added as well as .zip files for the
    boardhouse.
    [Finishline Controller.brd, Finishline Controller.sch, Finishline Display.brd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]
2018-06-04 add the Illustrator files for the Finishline Display fronts.
    [Finishline-Display-Transluzent.dxf]
2018-06-10 provide a test sketch for the RGB LEDs to test the circuits,
2018-06-15 provide a test sketch for the hardware
    This sketch runs a test, how fast the loop() is run and if the
    laser bean breaks are detected properly. With 18ms cycle time
    this seems sufficient at this moment. More tests are necessary.
2018-06-25 fix the initialisation error of the TM1637.
    The speedtest example runs now standalone and with the hardware demo
    switch, the operation of the finishline controller can be toggled
    between race demo or LDR setup.
    [PCF8574.cpp, TM1637.cpp, finishline-controller.ino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]
2018-07-02 switch the linting from eslint to standard
    Fixed the test specifiations and changed the linting from eslint to
    standard. Needed adaptations of the tests have been made by adding
    environments to package.json, define globals there and use the
    chai-dirty module.
    [index.js]
2018-07-02 add preliminary JSON handling class
    This is the groundwork for the JSON communication. It is capable to
    instantiate a protocol object with the serial port on which it is
    communicating. Three messages from the protocol have been implemented.
2018-07-04 fix serial communications, add further enhancements to the receive functions
    [PWDProtocol.h, finishline-controller.ino]
2018-07-05 refactor the main loop and lay the foundation for the state machine
    In demo mode it progresses from IDLE to HEATSETUP when receiving
    the corresponding message and starts to emit random setup messages
    for the cars.
2018-07-05 Serial communication final - 1 (#2)
    * initial changes for serial communication from bridge
    * boilerplate for public functions and message receive procedures
    * initial changes for serial communication from bridge
    * boilerplate for public functions and message receive procedures
    * Introduce constants, msg queue handling, msg queue timer
    * Introduce acknowledge message handling
    * Implements lane status detection messages
    * Implements heat update messages
    * Implement heat initialization message
    * Update update heat message handling
    * Fix car detection handling
    * Implement logic for updating Highscore board
    * Correct logical and syntax errors
    * Fix syntax er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
    [index.js]
2018-07-05 finalizes demo mode for INIT, HEATSETUP and RACING states
    The microcontroller now accept heat setup messages on the serial port
    and configures the heat. It emits random car detect messages and
    converges to a complete setup. After receiving the go command
    it simulates a race with random winners and emits progress messages
    on the serial port.
2018-07-06 complete the firmware for the finishline w/o startgate communication
    All commands and states have been implemented and tested. The track
    can run in demo mode, generating random messages and also in race mode.
    Control is over the serial interface to the bridge. Debug output is
    sent to the native USB port of the Due.
2018-07-09 add communication with the startgate and 1st version of the startgate FW
    The startgate has been upgraded to an Arduino Mega, since the displays
    and RFID Readers have taken up too much RAM space.
    [PWDSkinnyProtocol.cpp, PWDSkinnyProtocol.h, PWDStartGateDisplayReader.cpp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]
2018-07-09 release version 0.1.0 for both firmwares.
    All commands are available for both controllers. Needs a burn-in test
    over several hours. Demo Mode messages now match actual messages from
    a heat.
    [PWDProtocol.h, PWDSkinnyProtocol.cpp, PWDSkinnyProtocol.h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]
2018-07-11 Add raceconfigs and defines databases for the bridge
    There was a small change to send car detect messages during demo
    also to the Raspberry Pi. The bridge/doc directory contains
    predefined race configurations for 28-40 cars. The doc directory
    also contains the definitions of the databases used by the bridge.
2018-07-12 Implementation of discussed changes (#3)
    * Fix synt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
    [index.js]
2018-07-12 REST enpoint for cars (#4)
    * Fix syntax error
    *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
    [index.js]
2018-07-13 REST endpoint for heats (#5)
    * Start implementing rest interface for heat information
    * Finish first implementation for REST endpoint for heats
2018-07-13 Add timeout support to finishline and add a create heat REST endpoint
2018-07-13 Fix the initialisation of heat time and score to zero
    [index.js]
2018-07-13 Add support for heat init and heat start commands
2018-07-13 Correctly initialize the Race Number
    [index.js]
2018-07-13 Change default serial port and Heat Initialization
2018-07-15 Fix communication between track and bridge
    Added lots of try/catch handlers to avoid the bridge to throw ever
    completely, as this will reset the serial port. Started to change
    the highscore and leaderboard routines, as it may happen that a
    heat must be restarted and so the cumulative scores and times must
    be recalculated from all heat results. Added support to re-create
    a missing or corrupt heat of a race.
    [finishline-controller.ino, index.js]
2018-07-15 Fix leaderboard updates during race progress and race finish
    Also add some 3D files for the cover of some hardware parts.
    Leaderboard REST call returns now a sorted array instead of
    the raw object.
    [Made With.stl, Made-Cover-left.stl, Made-Cover-right.stl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]
2018-07-16 Add highscore handling also for incremental progress reports
    [Herzchen.stl]
2018-07-16 fix type regarding the startAt property and adds public routes
    [index.js]
2018-07-16 Fix leaderboard scoring and path auth exemption
    [index.js]
2018-07-16 Fix current and next heat marking and retrieval
    [index.js]
2018-07-16 Fix error, when multiple heats were marked as current or next
    [index.js]
2018-07-16 Resolve a naming conflict caused by the last change
    [index.js]
2018-07-16 Repair non-fitting Mae With Love Cover and add raceconfigurations
    [Made With - Cover.stl, Made-Cover-left.stl, Made-Cover-right.stl]
2018-07-17 Update live.html (#9)
    Added status info on current race. Please set the correct CURRENT_RACE_STATUS_URL
2018-07-17 Fix incorrect car detection message in demo mode
    Improves also the handling of current/next heat requests.
    [finishline-controller.ino, index.js]
2018-07-17 Fix initialisation of races with multiple rounds
    [index.js]
2018-07-17 Fix heatnumbering for heats with multiple rounds
2018-07-17 Update live.html (#10)
    Added time and score to current race
2018-07-17 Fix heatnumbering and properties
2018-07-17 Fix leaderboard for offset heat indices
    [index.js]
2018-07-17 Fix status vs. state typo and url not ending with slash
    [index.js]
2018-07-17 Change the /display to show the results of the last heat
    Last heat remains displayed until a new heat gets marked as current.
2018-07-20 Fix a type filtering just finished heats and adds REST endpoint
    The new rest endpoint allows to get the results of a race in a
    format, that is better suited to be imported into a mongodb.
    [index.js]
2018-10-30 Correct a spelling mistake in the race export function
    [index.js]
2019-05-07 Update the node packages to a current state.
2019-05-08 initial WebSocket implementation (#12)
    * Resolve merge conflicts
    * Improve update handling of Race ID:
    * Add retry counter for unacknowledged messages
    * Add basic ability to establish WebSocket connection
    WebSocket sessions from clients to the server can be established by
    calling /websocket/attach with a ws upgrade message.
    In case any relevant data from serial module is received and processed,
    the client is notified via a dummy message.
    [index.js]
2019-05-08 Correct spelling mistake and add watershed to dependencies
    [index.js]
2019-05-13 Pull request to introduce change for scoring of heats (#14)
    * Fix the scoring issue for racers with the same time
    Racers who got the same racing time will now receive
    the same place within a heat (i.e. they will receive
    the same score). If this is the case, the subsequent
    place will be empty.
    For example:
    - 1st place: 8 points
    - 2nd place: 4 points
    - 2nd place: 4 points
    - 4th place: 1 points
    * Fix merge error from previous version
    * Fixes typo in bridge/serial/index.js
    * Fixes linting errors
    [index.js]
2019-05-22 Add direct push of data to websocket clients (#15)
    Every time a displayable data object is changed, the new data
    is directly pushed to all attached websocket clients.
2019-05-28 Correctly initialize the websocket data structure
    [index.js]
2019-06-13 Fix change of updateUser function renaming
    [index.js]
2019-06-20 Switch out websocket module because of timeouts on Windows
2019-06-23 Fix some bugs introduced by the introduction of rounds into raceconfig
    [index.js]
2019-06-24 Fix typos and error logging
    [index.js]
2019-06-28 Fix deletion of heats while saving a race with less cars than before

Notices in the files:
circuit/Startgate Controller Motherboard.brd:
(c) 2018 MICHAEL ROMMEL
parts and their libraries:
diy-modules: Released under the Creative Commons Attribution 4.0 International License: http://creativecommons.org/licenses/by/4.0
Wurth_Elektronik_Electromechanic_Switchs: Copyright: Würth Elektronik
